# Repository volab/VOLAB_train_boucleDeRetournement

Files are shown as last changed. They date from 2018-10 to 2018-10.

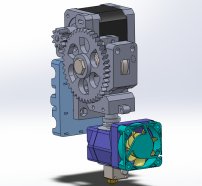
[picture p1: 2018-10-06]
03-conception/boucleRetournementConception/images/VOLABTrainBr_Image1.jpg

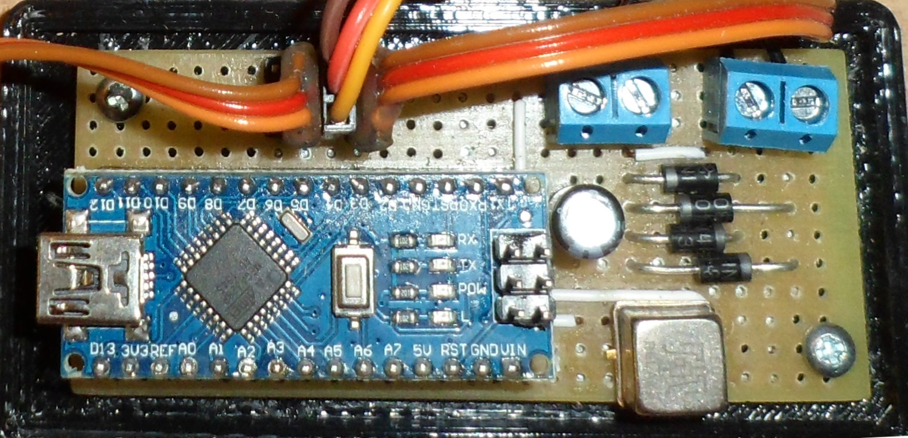
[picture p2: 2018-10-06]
03-conception/boucleRetournementConception/images/VOLABTrainBr_carteMereDessuPhoto.JPG

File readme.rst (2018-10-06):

=======================================================
Informations générales VOLAB_train_boucleDeRetournement
=======================================================

:Auteur:            `MajorLee95 <https://github.com/MajorLee95>`_
:Projet:             VOLAB_train_boucleDeRetournement
:dépôt GitHub:       https://github.com/volab/VOLAB_train_boucleDeRetournement
:documentation:      http://www.vorobotics.com/wiki/index.php?title=Boucle_de_retournement   
:Licence:            CC0
:Liens:              https://creativecommons.org/licenses

Description
===========

 Le réseau de train électrique miniature du VoLAB comporte une boucle.
 
 Il s'agit ici de traiter le court-circuit qui se produit au passage de cette boucle.

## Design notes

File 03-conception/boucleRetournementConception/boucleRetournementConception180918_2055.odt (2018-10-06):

# VoLAB

# Association VoRoBoTics

Date : 20/08/2018

Auteur : J.SORANZO

Relecteur : Gilbert, Daniel, Stéphane

Thème: Réseau ferroviaire modèle réduit H0

Projet : boucle de retournement du Petit Train du VoLAB

# Problématique

Le réseau ferroviaire en modèle réduit du VoLAB comporte une boucle. Or dans ce genre de boucle, se produit un phénomène bien connu des modélistes ferroviaires une inversion de polarité des voies.

Ce phénomène est très bien illustré et décrit sur internet en particulier sur le site : Ho Ptit Train (http://www.ho-ptit-train.be/Html/cablage_06.html) dont je reproduit ici l’illustration.

Illustration 1: Principe de la boucle de retournement

Celle du Petit Train du VoLAB :

Illustration 2: La boucle du Petit Train du VoLAB

Sans intervention, cette construction débouche sur un court-circuit entre les 2 voies. Il n’y a pas d’autres possibilité que de couper physiquement les rails à un endroit ou à un autre de cette boucle.

Nous avons choisi de couper le réseau après l’aiguillage 4184 du centre.

Illustration 3: Coupure du réseau Petit Train du VoLAB

Cette coupure n’est portant pas suffisante. En effet lorsqu’une locomotive arrive à cet emplacement, lorsque son bogie avant passe la coupure, elle crée à nouveau le court-circuit. Il faut donc concevoir une boucle de retournement.

# Architecture

Afin de résoudre ce problème, plusieurs solutions sont envisageables. Le site Ho Petit Train fournit un certain nombre de solutions. Compte-tenue du prix faible de ces derniers, nous avons décider de créer une solution à base de micro-controleur. Nous nous sommes orientés vers un clone d'ARDUINO Nano que nous avons déjà utilisé dans notre commande d'aiguillage. Cela nous à permis de conserver le même principe de carte mère et de conserver le support imprimé en 3D. L'alimentation se fait par la voie principale grâce à un pont redresseur et un condensateur de filtrage.

Dans le principe, nous avons décidé de faire une boucle de retournement sans court ciruit. Nous avons utilisé 3 capteurs de présence: 1 à l'entrée de la boucle, 1 dans la boucle et 1 à la sortie. 3 capteurs sont nécessaires parceque cette boucle est bi-directionnelle. Les capteurs d'entrée et de sortie changent de rôle selon le sens de la loco. Nous détectons la loco à l'entrée de la boucle, nous "alignons" les polarités des voies (si besoin) à l'aide d'un relais électro-mécanique à 2 contacts repos/travail. Lorsque la loco est détectée à l'intérieur de la boucle, nous pouvons permuter les polarités des voies. Et enfin, nous détectons la sortie de la loco de la boucle mais cela n'est pas vraiment nécessaire sauf pour remettre le sytème en état d'attente. Ce schéma de fonctionnement implique que le convoit ne fasse pas marche arrière lorsqu'il a franchi le deiuxième capteur, celui à l'intérieur de la boucle.

Illustration 4: position des capteurs et des coupures

# Choix du capteur

Nous avons exploré plusieurs types de capteurs de détection de présence de la loco. Cela peut être un simple contact placé sous la voies, un ILS, une barrière infra-rouge et nous avons même envisagé un capteur à ultra-son type SFR-04 (un poil trop volumineux) ou encore une barrière constitué d’une diode laser et d’une LDR. Bref tout type de capteur fonctionnant en mode tout ou rien qui change d’état au passage d’une locomotive. Notre choix final s’est porté sur un capteur à effet hall suffisamment petit pour être logé sous la voie.

Illustration 5: Capteur 1 | Illustration 6: Capteur 2 et Electronique | Illustration 7: Capteur 3

S’est alors posé la question du choix du capteur à effet hall en lui-même. Nous avons découvert à nos dépends ce que signifiaient les termes unipolaire/bipolaire/linéaire figurant dans les datasheets de ces derniers.

Unipolaire : le capteur ne détecte un champ magnétique que dans un seul sens. C’est à dire que si on met l’aimant à l’envers : plus de détection…

bipolaire : le capteur détecte les champs dans les 2 sens

linaire : le capteur ne fonctionne pas en mode tout ou rien mais mesure réellement la valeur du champ magnétique, il faut alors souvent faire une mesure en analogique et faire un comparateur logiciel dans le code de l’ARDUINO.

Ah oui détail important ce choix impose de fixer un aimant sous la loco. Aimant qu’il faut choisir avec soin en fonction du capteur. En effet, on trouve dans la datasheet de ces derniers la valeur du champ à partir de laquelle ils réagissent. Le problème est que cette information est plus difficile à trouver côté aimants surtout ceux vendus sur le marché chinois. Heureusement, il est des sites plus sérieux qui fournissent cette information mais au prix d’un coût plus élevé naturellement comme par exemple https://www.supermagnete.fr.

Illustration 8: tableau de conversion Tesla en Gauss

Après bien des essais, nous avons choisi un A1104 du fabricant Allegro. De part les faibles dimensions du boîtier, il nous semble facilement dissimulable entre les voies.

# Machine d’état

Nous avons basé le fonctionnement de notre boucle de retournement sur la machine d'état suivante que nous avons codé dans un ARDUINO Nano comme dit plus haut dans cet article.

Illustration 9: machine d'état

Les états 0 à 5 correspondent au parcours du train dans le sens capteur 1 (C1) capteur 3 (C3) en passant par le capteur 2 (C2) naturellement.

Les étapes 0, 6 à 10 correspondent au parcours de la boucle dans l'autre sens.

L'état de repos est, vous l'aurez sans doute compris, l'état 0.

La transition de l'état 1 vers l'état 0 n'a pas été implémentée. Elle était destinée à prendre en compte le train qui après avoir franchis le capteur 1 ferait marche arrière. Pour faire simple, nous nous interdisons les marches arrières dans la boucle de retournement.

# Le code ARDUINO

//
// retour loop
// VoLAB
// mai 2018
// CC-0
//
#define C1PIN 5
#define C2PIN 4
#define C3PIN 3

#define RELAISPIN 2
#define LEDRELAIS 13

int state;

void setup(){
pinMode( C1PIN, INPUT_PULLUP );
pinMode( C2PIN, INPUT_PULLUP );
pinMode( C3PIN, INPUT_PULLUP );
pinMode( RELAISPIN, OUTPUT);
pinMode( LEDRELAIS, OUTPUT);
Serial.begin(9600);
Serial.println("pret");

}

void loop(){
// inversées à cause du INPUT_PULLUP
int C1 = !digitalRead(C1PIN);
int C2 = !digitalRead(C2PIN);
int C3 = !digitalRead(C3PIN);
char chaine[256];
// sprintf( chaine, "C1 : %d, C2 : %d, C3 : %d", C1, C2, C3);
sprintf( chaine , "etat : %d", state);
Serial.println( chaine );

//Machine d'état
switch (state){
case 0:
if (C1) state = 1;
if (C3) state = 6;
break;
case 1: if (!C1) state = 2; break;
case 2: if (C2) state = 3 ; break;
case 3: if (!C2) state = 4 ; break;
case 4: if (C3) state = 5 ; break;
case 5: if (!C3) state = 0 ; break; //le train est sorti en C3
case 6: if (!C3) state = 7 ; break;
case 7: if (C2) state = 8 ; break;
case 8: if (!C2) state = 9 ; break;
case 9: if (C1) state = 10 ; break;
case 10: if (!C1) state = 0 ; break;
default:
state = 0;
break;
}

//Décodage des états
if ( state == 4 | state == 6 ){
digitalWrite( RELAISPIN, HIGH);
digitalWrite( LEDRELAIS, HIGH);
}
if (state == 5 | state == 9){
digitalWrite( RELAISPIN, LOW);
digitalWrite( LEDRELAIS, LOW);
}

}

Ce sketch est très simple. Il débute par l'assignation des broches de connections des 3 capteurs, de la sortie relais et d'une sortie d'affichage de l'état du relais.

Dans la déclaration de la fonction setup, on réalise la configuration des dites broches. Seule petite subtilité, les broches d'entrées des capteurs sont configurées en INPUT_PULLUP ce qui permet de se passer de résistances de tirage extérieures. La contre-partie est que le niveau actif de l'enrée est 0 au lieu de 1.

Ensuite vient la déclaration de la fonction loop qui commence par lire l'état des 3 capteurs en les inversant ( rôle du ! devant les digitalRead() ). Ensuite vient la machine d'état qui gère les transitions entre les états conformément à l'illustration 9 machine d'état. Et enfin la partie décodage des états pour piloter le relais (et la LED).

# Schémas

## Carte mère et ARDUINO Nano

Relais pinout

Illustration 10: Brochage du relais (vue de dessous) | Illustration 11: Pinout du relais

Transistor 2N7000 pinout

Illustration 12: 2N2700 pinout

Ci-dessous le schéma de la petite carte mère que nous avons réalisé pour accueillir les quelques composants nécessaires... Nous avons commis ça grâce à Kicad.

Illustration 13: Schéma de la carte mère

Nous avons réalisé un routage même si nous n'avons pas fait de pcb et l'avons fait avec une carte VEROBOARD:

Comme le VEROBOARD utilisé est simple face, les autres couches du PCB sont des straps réalisés en fils de cuivre.

Illustration 14: Le PCB de la carte mère

Illustration 15: Carte mère en vue de dessus | Illustration 16: Carte mère en vue de dessous

## Raccordement aux voies

J1 est le connecteur principal et doit être raccordé à la voie principale.

J5 doit être raccordé aux rails de la boucle.

Il y a une petite subtilité : la vis de droite de J1 doit être raccordée au rail du même côté que la vis de droite de J5. Exemple au rail de droite – même si il n'y a pas vraiment ni de rail de droite, ni de rail de gauche étant donnée que les trains peuvent circulés dans les 2 sens. Il faut bien se fixer une convention à un moment ou un autre...

## Nomenclature

Désignation | Ref fab | Fabricant/fournisseur | Repère
Clone ARDUINO nano | NANO V3 | Banggood | U1
Relais | 114D | Teledyn | R1
Diode | 1N4004 | ? | D1 à D4
Transistor | 2N7000 | On semi | Q1
Condensateur | 100uF/16V | ? | C1
Connecteurs 2cts | Pas 5.08 à vis | Banggood | J1, J5
Connecteur 3cts | Pas 2.54 barette | Banggood | J2, J3 et J4
PCB | Plaque à pastille carrée | Radiospares part. | -
2 vis | M2,5x6 | Bricovis | -

# Support de carte imprimé en 3D

Illustration 17: Support

Il s'agit d'un support très simple qui permet par la suite de fixer la carte au réseau grâce à 2 vis. Nous l'avons réutilisé du projet de commande d'aiguillage (d'où l'insription DCC Turnout). Sa conception bénéficie d'un de nos autres projets : Bobies (http://www.vorobotics.com/wiki/index.php?title=BOBies).

On y fixe la carte mère grâce à 2 vis de 2.5 x 6 ( PLATCBZ02.5/006ZN disponibles chez BRICOVIS (https://www.bricovis.fr/std/accueil.php) )

# Fichiers sources

Source ARDUINO

Source du présent article au format open document

Version pdf

Schéma de cablage

Source Inkscape de la machine d’état

Source du support mécanique Fusion360

Les source kicad de la carte mère

datasheet du relais

# Licence

Ce document est mis à disposition selon les termes de la Licence Creative Commons Attribution 4.0 International (http://creativecommons.org/licenses/by/4.0/).

CC0

# Bibliographie

Ho Ptit Train

http://www.ho-ptit-train.be/Html/cablage_06.html

# webographie

http://fr.wikipedia.org/wiki/Licence_Creative_Commons

Kicad

http://kicad-pcb.org/

http://banggood.com (dealer de goodies!)

NANO V3 (https://www.banggood.com/ATmega328P-Nano-V3-Controller-Board-Compatible-Arduino-p-940937.html?rmmds=search) à 2.23€ (au 18/9/18) à condition de choisir « Ships from CN Warehouse »

On-semi (datasheet transistor)

http://www.onsemi.com/

Teledyn (relais)

http://www.teledyne.com/

Bricovis

https://www.bricovis.fr/std/accueil.php

# Rédaction en langue française

Partant du constat de terrain qu'une énorme masse d'information concernant les sujets qui nous intéressent comme entre autres l'impression 3D n'étaient disponibles que dans la langue de Shakespeare et que de nombreuses personnes dans notre entourage ne maîtrisaient pas la dite langue et soucieux de diffuser encore plus l'information, nous avons pris le parti, au VoLAB, de rédiger nos documents de préférence en langue française.

# VoLAB

Un mot sur le VoLAB. VoLAB est un fablab implanté à environ 30km au nord-ouest de Paris dans la commune de Vauréal dans l'agglomération de Cergy Pontoise. Il est animé par l'association VoRoBoTics.

Site internet www.vorobotics.com

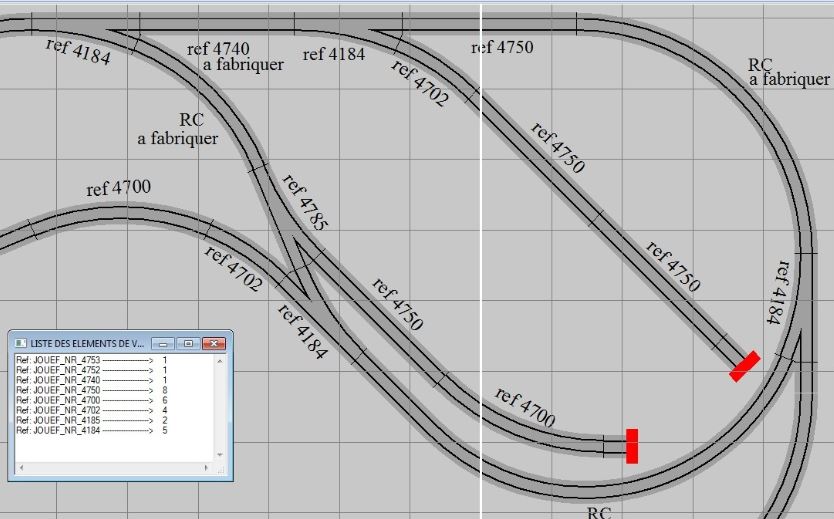
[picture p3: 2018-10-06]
03-conception/boucleRetournementConception/images/VOLABTrainBr_boucleVueEnsemble.JPG

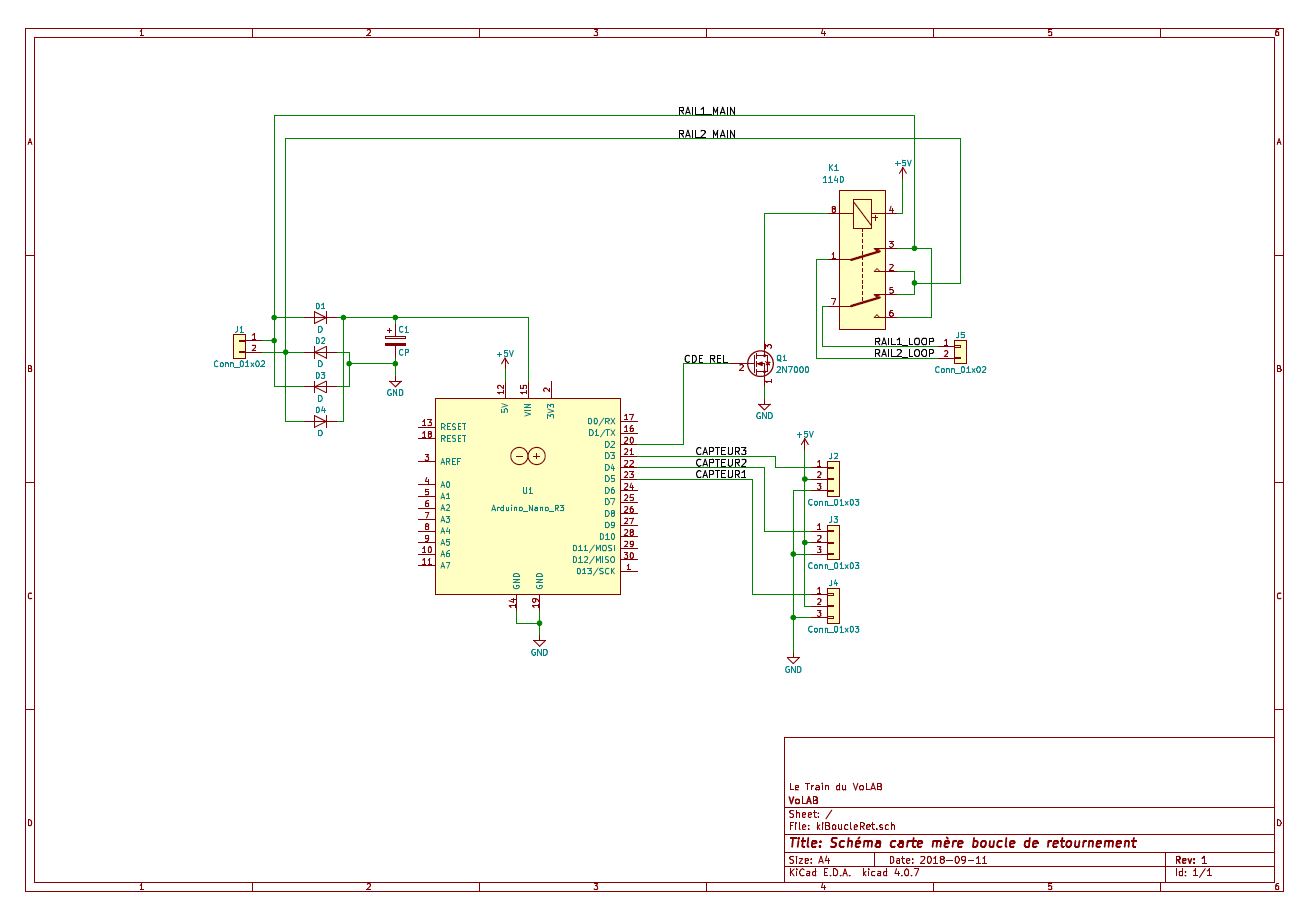
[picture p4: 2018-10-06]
03-conception/boucleRetournementConception/images/VOLABTrainBr_schemaCarteMere.JPG

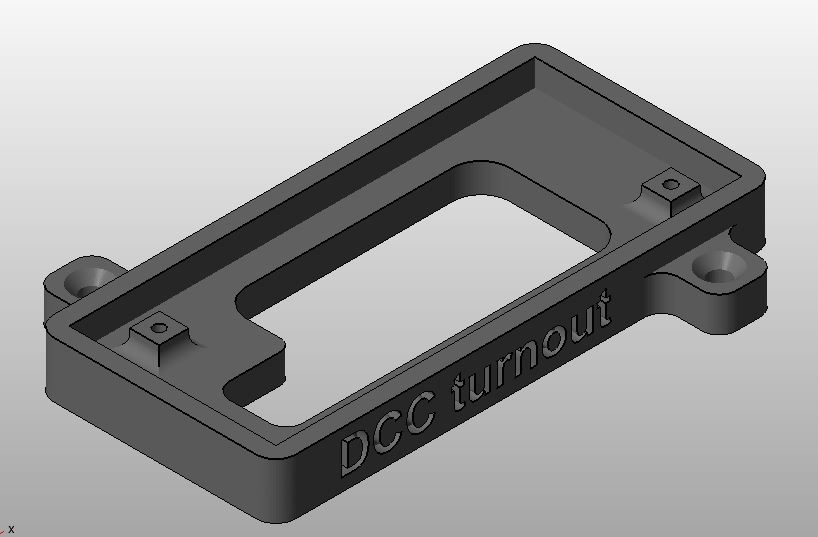
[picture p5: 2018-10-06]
03-conception/boucleRetournementConception/images/VOLABTrainBr_support.JPG

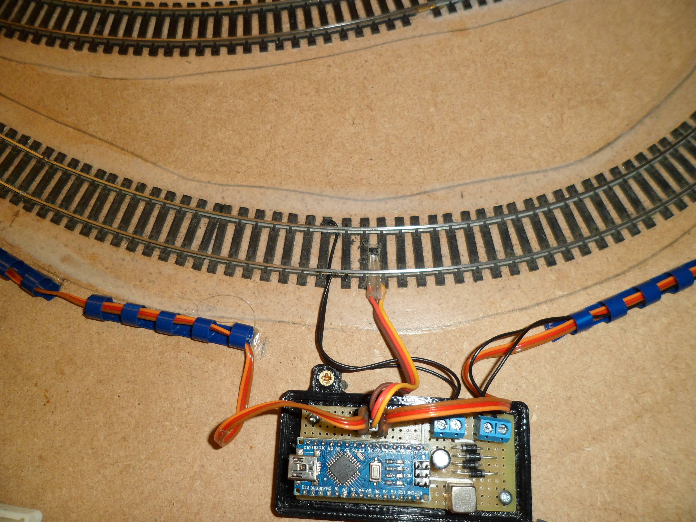
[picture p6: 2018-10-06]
03-conception/boucleRetournementConception/images/VOLABTrainBr_photoCapteur2EtElectronique.JPG

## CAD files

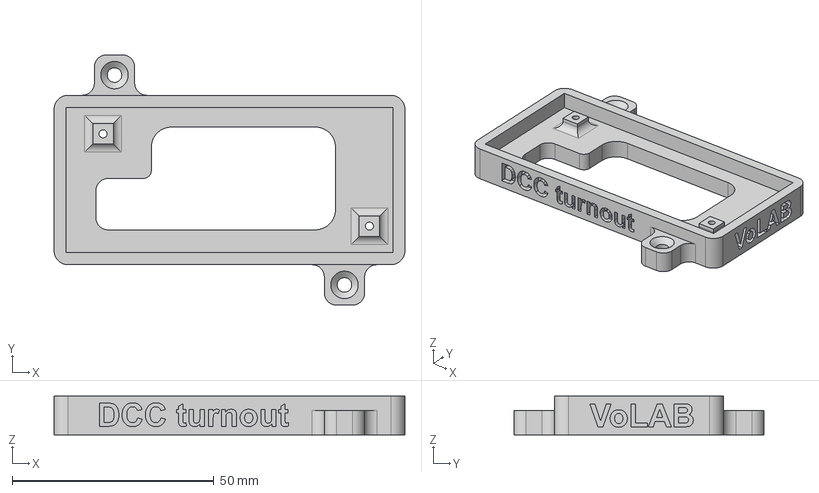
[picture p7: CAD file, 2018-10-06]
04-realisation/03-cao_3D/supportCarteDecodeurAiguillage_v4.step
87.0 x 62.0 x 9.60 mm

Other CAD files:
04-realisation/dccTurnout.stl
04-realisation/03-cao_3D/supportCarteDecodeurAiguillage_v4.f3d

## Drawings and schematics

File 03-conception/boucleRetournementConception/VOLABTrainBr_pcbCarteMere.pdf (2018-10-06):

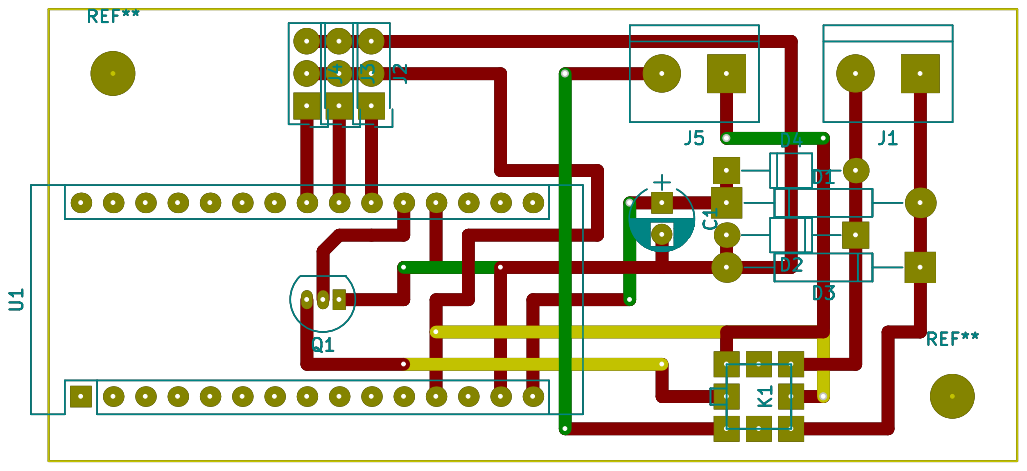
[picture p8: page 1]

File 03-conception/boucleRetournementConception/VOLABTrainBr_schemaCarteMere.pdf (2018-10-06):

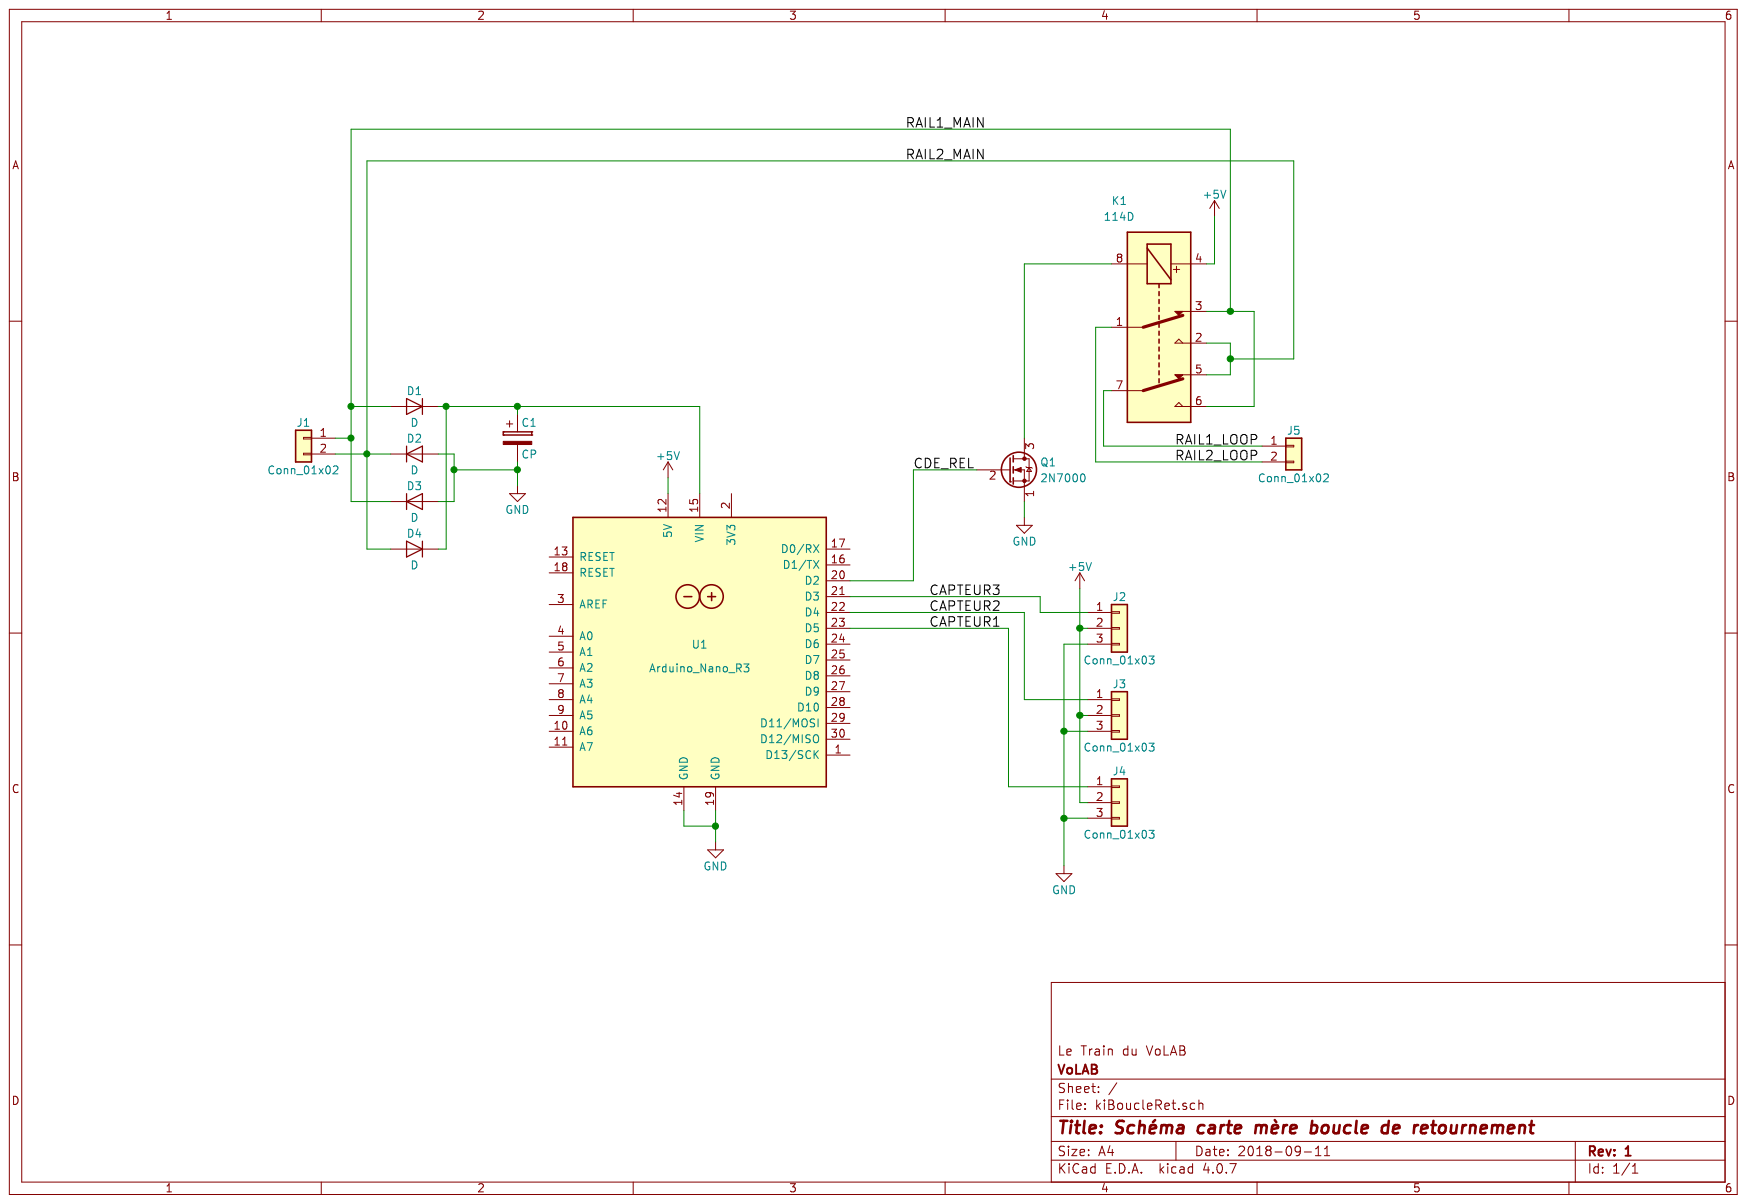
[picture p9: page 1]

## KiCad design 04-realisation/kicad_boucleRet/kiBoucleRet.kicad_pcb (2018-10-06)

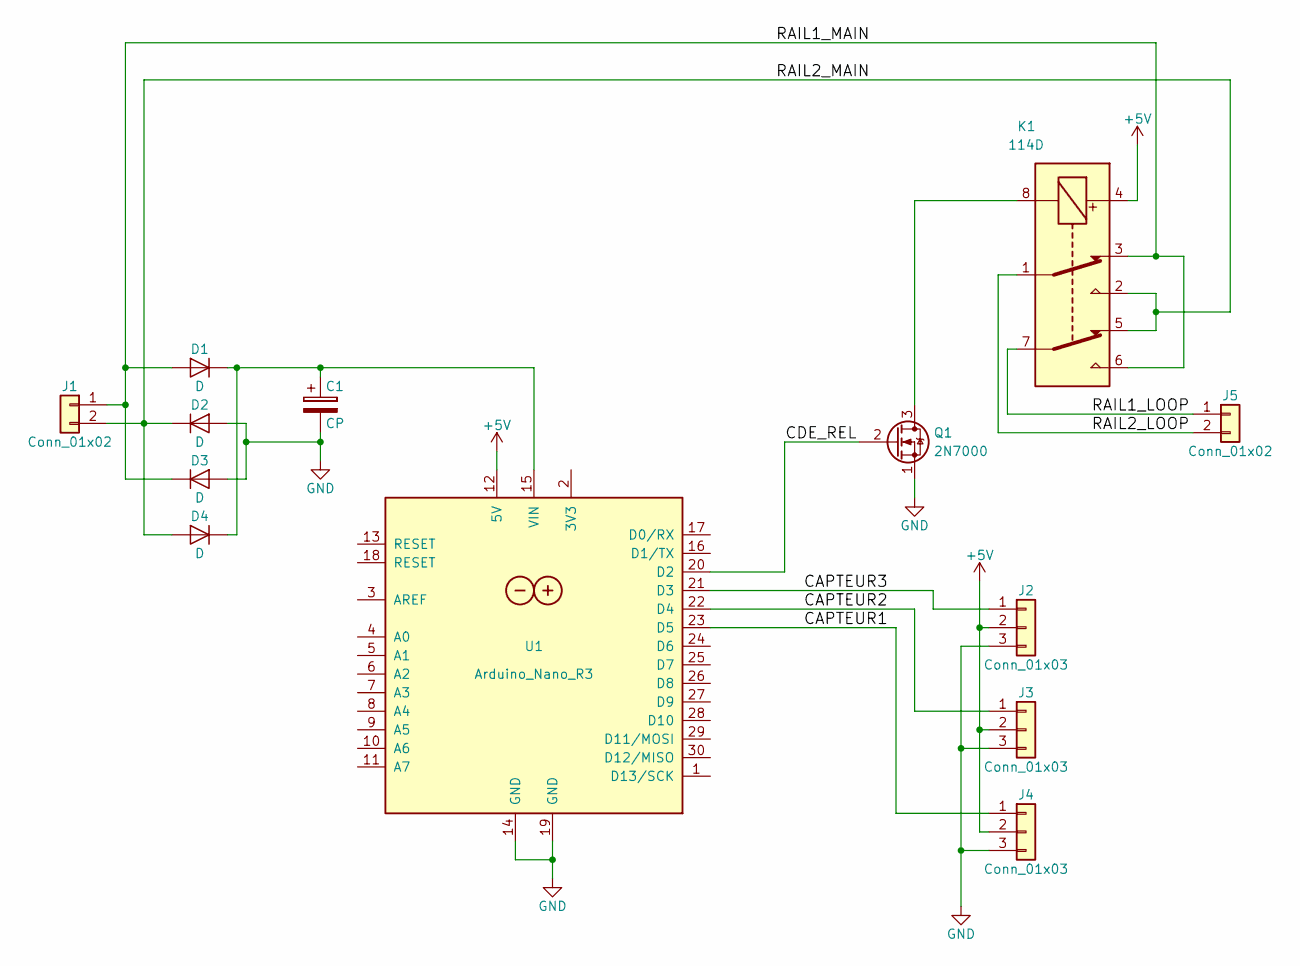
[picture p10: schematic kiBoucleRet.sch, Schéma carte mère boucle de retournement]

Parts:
C1: CP; CP_Radial_D5.0mm_P2.50mm
D1, D3: D; 1N4004_P15.24mm_Horizontal
D2, D4: D; D_T-1_P10.16mm_Horizontal
J1, J5: Conn_01x02; bornier2
J2, J3, J4: Conn_01x03; SL-103-X-XX_1x03
K1: 114D; R114D_ronde
Q1: 2N7000; TO-92_Inline_Narrow_Oval
U1: Arduino_Nano_R3; Arduino_Nano

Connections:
+5V: J2.2, J3.2, J4.2, K1.4, U1.12 (5V)
/CAPTEUR1: J4.1, U1.23 (D5)
/CAPTEUR2: J3.1, U1.22 (D4)
/CAPTEUR3: J2.1, U1.21 (D3)
/CDE_REL: Q1.2 (G), U1.20 (D2)
/RAIL1_LOOP: J5.1, K1.7
/RAIL1_MAIN: D1.2 (A), D3.1 (K), J1.1, K1.3, K1.6
/RAIL2_LOOP: J5.2, K1.1
/RAIL2_MAIN: D2.1 (K), D4.2 (A), J1.2, K1.2, K1.5
GND: C1.2, D2.2 (A), D3.2 (A), J2.3, J3.3, J4.3, Q1.1 (S), U1.14 (GND), U1.19 (GND)
unnamed: C1.1, D1.1 (K), D4.1 (K), U1.15 (VIN)
unnamed: K1.8, Q1.3 (D)

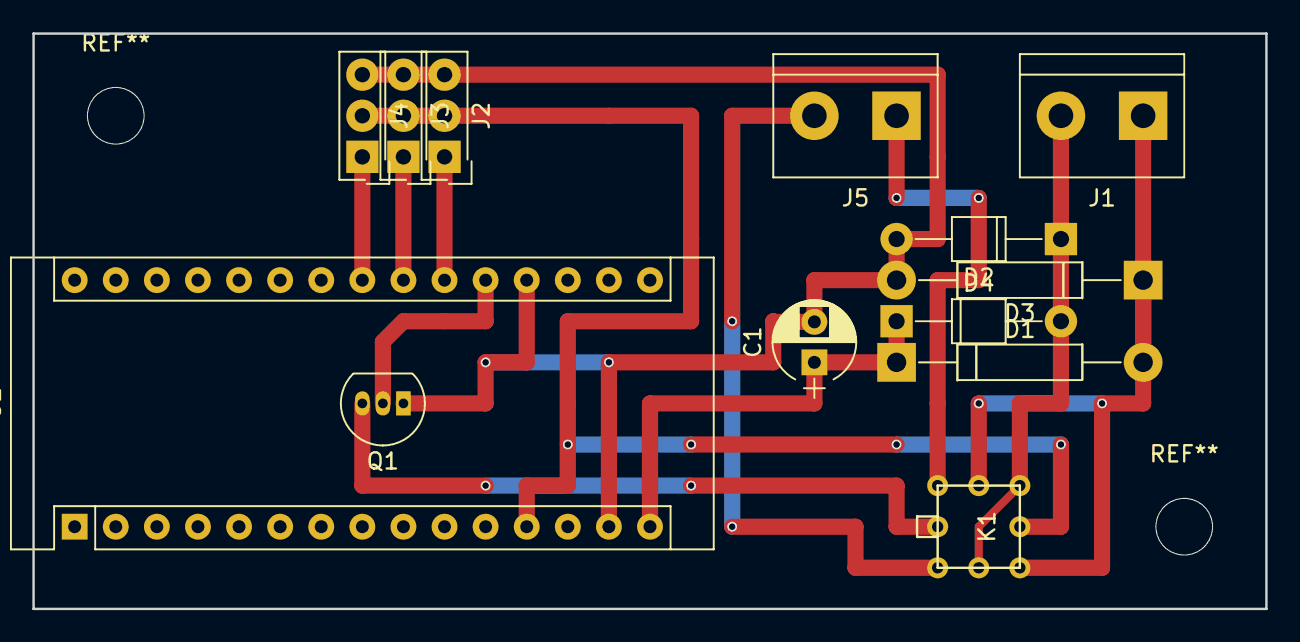
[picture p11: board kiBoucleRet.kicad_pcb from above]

Board: 4 copper layers, 76.2 x 35.6 mm, 13 parts (0 on the bottom side), 12 nets.

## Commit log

2018-10-06 ajout kicad submodule
2018-10-06 deuxième tentative d'ajout de 04-realisation/kicad_boucleRet dans le dépot distant
2018-10-06 troisieme tentative ajout kicad projet
    [kiBoucleRet.kicad_pcb, kiBoucleRet.sch]
2018-10-06 Ajout des fichiers CAO
    [supportCarteDecodeurAiguillage_v4.f3d, supportCarteDecodeurAiguillage_v4.step]
2018-10-06 ajout du pdf de l'article du wiki
